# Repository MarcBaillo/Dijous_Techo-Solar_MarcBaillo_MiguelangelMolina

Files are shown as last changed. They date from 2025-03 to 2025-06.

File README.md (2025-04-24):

## Dijous_Techo-Solar_MarcBaillo_MiguelangelMolina
Proyecto de Herramientas de Diseño del Techo Solar (Jueves).

# Autores
- Miguelangel Molina(@MiaMoSaN)
- Marc Baillo (@MarcBaillo)

## Objectivos del proyecto

El objetivo que tenemos es conseguir diseñar un techo solar que estara formado por un microcontrolador, 2 motores que controlaran la apertura con final de carrera y el movimiento de la cortina, un sensor que evite atrapamientos y una luz ambiental producida por un LED RGB. Todo esto estara implementado en una PCB, pasando por las fases de diagrama de bloque, que luego pasar al esquematico y alfinal al layout, para luego evaluarlo y hacer unos presupuestos de cuanto valdra crear la placa.

## Requisitos i especificaciones:

- Diseño integral de un techo solar controlado por microcontrolador.
- Implementación de un motor de apertura con final de carrera.
- Integración de un motor de la cortina.
- Luz ambiental RGB.
- Integración de un sensor digital para evitar que atrapamientos.

## Diagrama de bloque

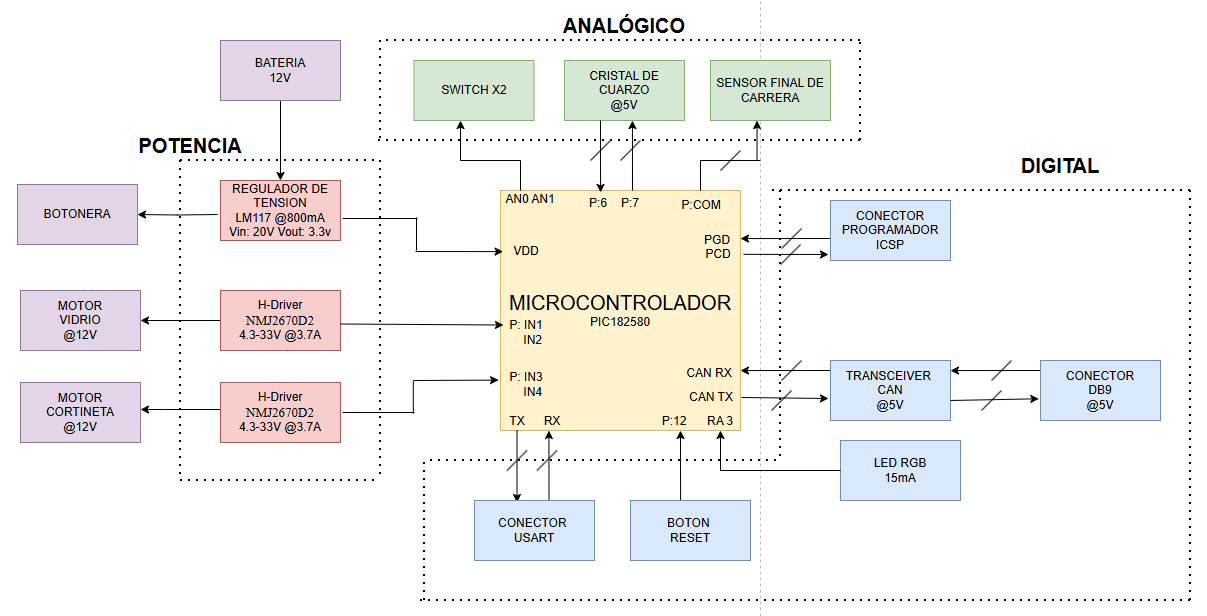
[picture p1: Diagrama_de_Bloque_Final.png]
Diagrama de Bloque


## Tabla de componentes
| Descripción | Manufacturer Number | Descripción | Datasheet | Proveidor | Unidades | Precio Unitario |
|:---:|:---:|:---:|:---:|:---:|:---:|:---:|
| Microcontrolador | PIC18LF2580-I/SO | Procesador que actúa como cerebro de control del circuito | [Datasheet](https://ww1.microchip.com/downloads/aemDocuments/documents/OTH/ProductDocuments/DataSheets/39637d.pdf) | DigiKey | 1 | 9,2€ |
| Regulador de tensión | LM1117DT-3.3/NOPB  | Dispositivo que hace que la tensión de entrada pase de 12V a los que necesita el microcontrolador (3,3V) | [Datasheet](https://www.ti.com/lit/ds/symlink/lm1117.pdf?ts=1710745623625&ref_url=https%253A%252F%252Fwww.mouser.se%252F) | Mouser Electronics | 1 | 1,61€ |
| Conector | DB9  | Se ocupa de la conexión entre diferentes dispositivos |[Datasheet](https://www.mouser.es/datasheet/2/18/1/Cable_Glands_and_Cord_Grips-806485.pdf) | Mouser Electronics | 1 | 19,08€ |
| Oscilador | ECS-80-8-30-JGN-TR | Genera ondas de señales precisas| [Datasheet](https://www.mouser.es/datasheet/2/122/ecx_53r-1775695.pdf) | Mouser Electronics | 1 | 0,53€ |
| H-Driver | DRV8231ADDAR  | controla el sentido de giro de un motor | [Datasheet](https://www.ti.com/lit/ds/symlink/drv8231a.pdf?ts=1710753914026&ref_url=https%253A%252F%252Fwww.mouser.de%252F) | Mouser Electronics | 1 | 1,24€ |
| Transceiver | 	TCAN332DR  | Dispositivo que recibe y trtransmite datos |[Datasheet](https://www.ti.com/lit/ds/symlink/tcan332g.pdf?ts=1710924087476&ref_url=https%253A%252F%252Fwww.mouser.de%252F) | DigiKey | 1 | 2,83€ |
| LED RGB | LB Q39G-N1OO-35-1-5-R18  | LED que da luz ambiental al coche |[Datasheet](https://look.ams-osram.com/m/6e36864d019f51d4/original/LB-Q39G.pdf) | DigiKey | 1 | 0,2€ |
| Motor | D4387-12-ME  | Motores para poder abrir y cerrar el cristal o la cortina del techo | [Datasheet](https://transmotec.es/Download/Catalog/Transmotec-EN-DC-12W-450W-2022.pdf) | Transmotec | 2 | 345€ |
| Switch | SS-01GPD  | Dispositivos que controlan cuando es el final de carrera | [Datasheet](https://www.mouser.es/datasheet/2/307/en_ss-1509069.pdf) | Mouser Electronics | 1 | 1,27€ |
| Pulsador | MPB01-1B00-S-D  | Dispositivo que permite controlar el motor para que el techo o cortina se abra o se cierre  | [Datasheet](https://www.mouser.es/datasheet/2/670/mpb01-2474754.pdf) | Mouser Electronics | 2 | 3,14€ |
| Conector | ICSP  | Sirve para comunicarse con el exterior para programar el microcontrolador | [Datasheet](https://ww1.microchip.com/downloads/en/DeviceDoc/30277d.pdf) | DigiKey | 2 | 1,52€ |

## Historial de canvis 

| Data | Autor | Descripció |
|:---:|:---:|:---:|
| 20-03-2025 | Marc y Miguel | Creado el proyecto y escogido el diseño que se trabajara (Techo Solar) |
| 20-03-2025 | Marc y Miguel | Elección de componentes y presentación del proyecto (Sesión 1) |
| 20-03-2025 | Marc y Miguel | Creación de Diagrama de Bloque |
| 23-03-2025 | Marc | Cadlab y GitHub creado |
| 24-03-2025 | Miguel | Creación del Esquematico |
| 25-03-2025 | Marc | Simulaciones hechas |
| 26-03-2025 | Miguel | Modificación Diagrama de Bloque |
| 27-03-2025 | Marc | Creació del README |
| 27-03-2025 | Marc y Miguel | Modificación presentación proyecto (Sesión 2) |
| 31-03-2025 | Miguel | Creación Layout |
| 02-04-2025 | Marc | Simulación ADC hecha |
| 03-04-2025 | Miguel y Marc | Modificación presentación proyecto (Sesión 3) |
| 03-04-2025 | Miguel | Corrección errores Layout y Esquematicos |
| 09-04-2025 | Marc | Modificación Layout (acabar de poner vista 3D y packages bien) |
| 09-04-2025 | Marc |  Modificación presentación proyecto (Sesión 4)  |
| 10-04-2025 | Marc y Miguel |  Modificación presentación proyecto (Sesión 4)  |
| 10-04-2025 | Miguel | Finalización del Esquematico y del Layout |
| 10-04-2025 | Miguel | Reglas de diseño definidas |
| 23-04-2025 | Marc | Presupuesto hecho |
| 24-04-2025 | Miguel y Marc | Modificación presentación proyecto (Sesión presentación proyecto final) |

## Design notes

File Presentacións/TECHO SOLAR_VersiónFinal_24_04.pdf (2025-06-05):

# Proyecto: Techo Solar

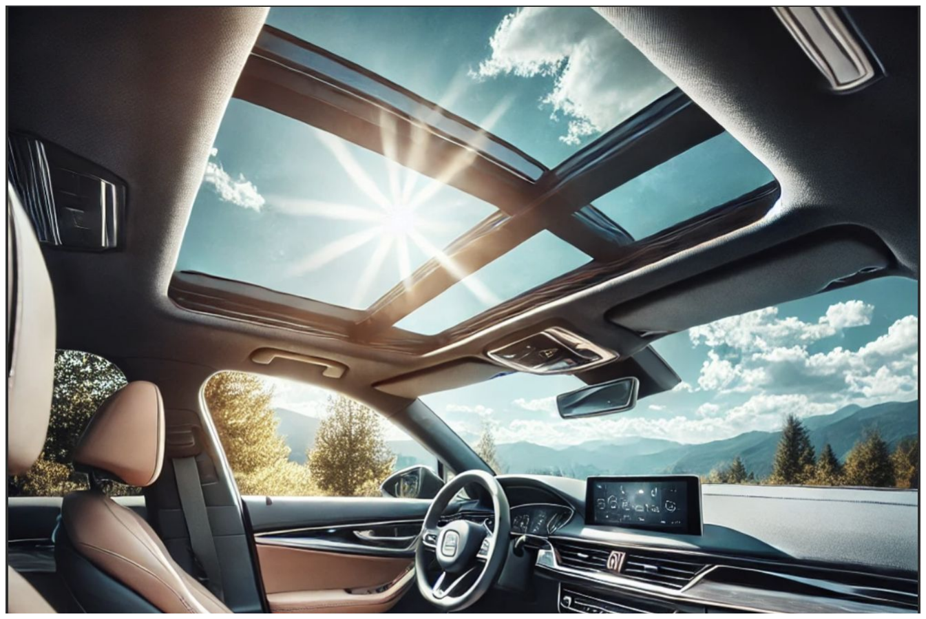
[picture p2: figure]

| Miguelangel Molina Marc Baillo

### Curso 2025 Grupo C

## El techo solar es un panel de vidrio o material translúcido ubicado en el techo de un automóvil que permite la entrada de luz y aire al interior del vehículo

## OBJETIVOS

Diseño integral de un techo solar controlado por microcontrolador.

Implementación de un motor de apertura con final de carrera.

Integración de un motor de la cortina.

Luz ambiental RGB.

Integración de un sensor digital para evitar que atrapamientos.

# Proyecto: Diseño del Techo Solar del coche

## DIAGRAMA DE BLOQUES

# Proyecto: Diseño del Techo Solar del coche

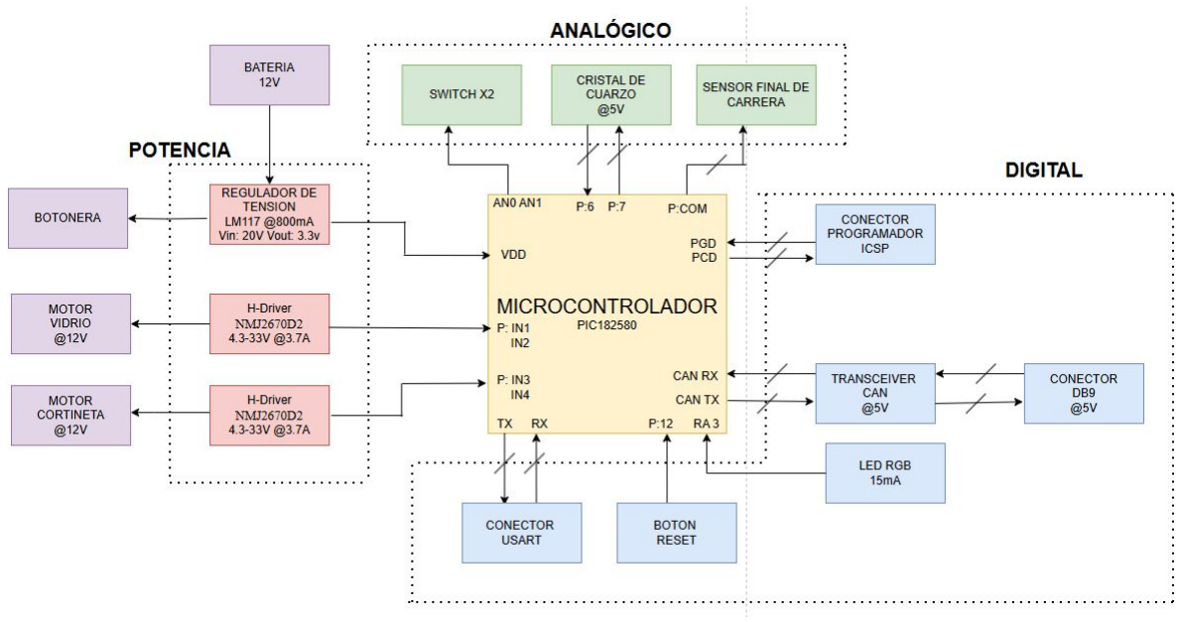
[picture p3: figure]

# Componentes

TIPO | COMPONENTES | DESCRIPCIÓN
POWER | | Las redes de potencia se refieren a los sistemas eléctricos que suministran energía eléctrica a los
ANALOG | Oscilador, Sensor final de carrera, | La información se transmite en forma de señales analógicas.
DIGITAL | Led Conectores de comunicación (Transceiver, db9, …) Microcontrolador, | Transmiten los datos en forma de

Driver motor
Regulador de tensión,
consumidores.

Botonera

Sensor de movimiento

bits, típicamente como 0 o 1.

# Proyecto: Diseño del Techo Solar del coche

# Proyecto: Diseño del Techo Solar del coche

COMPONENTES | UTILIDAD | CARACTERÍSTICAS | MODELO | DATASHEETS
Microcontrolador | Circuito programable que actuará como centro de control de todo el circuito. | Vmin = 2V Vmax = 5,5V I = 250mA
Regulador de tensión | Dispositivo que mantendrá o regulará un nivel de tensión constante. | Vmin = 3,3V Vmàx = 20V I = 1.2A
Conector | Conector que sirve para la
Oscilador | Permite la generación de señales
H-Driver | Permitirá el control de los motores. | V=4.3-33V Power supply = -0.5-35V Imax = 0-3.7A
PIC18LF2580 | Micro/datasheet (https://ww1.microchip.com/downloads/aemDocuments/documents/OTH/ProductDocuments/DataSheets/39637d.pdf)
LM1117CST-3.3 | Reg/datasheet (https://eu.mouser.com/datasheet/2/609/1117fd-2953685.pdf)
comunicación entre dispositivos. | — | DB9 | Conn/datasheet (https://www.mouser.es/datasheet/2/18/1/Cable_Glands_and_Cord_Grips-806485.pdf)
eléctricas de una alta precisión. | Frecuencia = 8 MHz | ECS-80-8-30-JGN-TR | Osc/datasheet (https://www.mouser.es/datasheet/2/122/ecx_53r-1775695.pdf)
L293DD | Driver/datasheet (https://www.alldatasheet.com/datasheet-pdf/view/22433/STMICROELECTRONICS/L293DD.html)

COMPONENTES | UTILIDAD | CARACTERÍSTICAS | MODELO | DATASHEETS
Transceiver | Se encarga de recibir datos y transmitirlos. | Vmin = 3V
Vmax = 3.6V | TCAN 332x | Tran/datasheet (https://www.ti.com/lit/ds/symlink/tcan332g.pdf?ts=1710924087476)
LED RGB | LED que dará luz ambiente | Forward current = 15 mA | LBQ39G | LED/datasheet (https://look.ams-osram.com/m/6e36864d019f51d4/original/LB-Q39G.pdf)
Motor cortina | Motor externo encargado de abrir o cerrar la cortina | Voltage=12 V
Motor final de carrera | Motor externo encargado de abrir o cerrar el techo | Voltage=12 V
I=2A | D4387-12-ME | Motor/datasheet (https://transmotec.es/Download/Catalog/Transmotec-EN-DC-12W-450W-2022.pdf)
I=2A | D4387-12-ME | Motor/datasheet (https://transmotec.es/Download/Catalog/Transmotec-EN-DC-12W-450W-2022.pdf)

# Proyecto: Diseño del Techo Solar del coche

COMPONENTES | UTILIDAD | CARACTERÍSTICAS | MODELO | DATASHEETS
Switch | Para el final de carrera. | 0.1A to 10.1A | B3F-4050 | Interr/datasheet (https://www.mouser.es/datasheet/2/307/en_b3f-1664344.pdf)
Pulsador cortina | Pulsador para abrir y cerrar
Conector | Para programar el
Pulsador cristal | Pulsador para abrir y cerrar
la cortina. | 14 mA | MPB01-1B33-S- D
Puls/datasheet (https://eu.mouser.com/datasheet/2/1628/mpb01-3510627.pdf)
microcontrolador. | — | ICSP | Conn/datasheet (https://ww1.microchip.com/downloads/en/DeviceDoc/30277d.pdf)

# Proyecto: Diseño del Techo Solar del coche

el cristal del techo. | 14 mA | MPB01-1B33-S- D
Puls/datasheet (https://www.mouser.es/datasheet/2/670/mpb01-2474754.pdf)

# Proyecto: Simulación LTSpice Motor DC

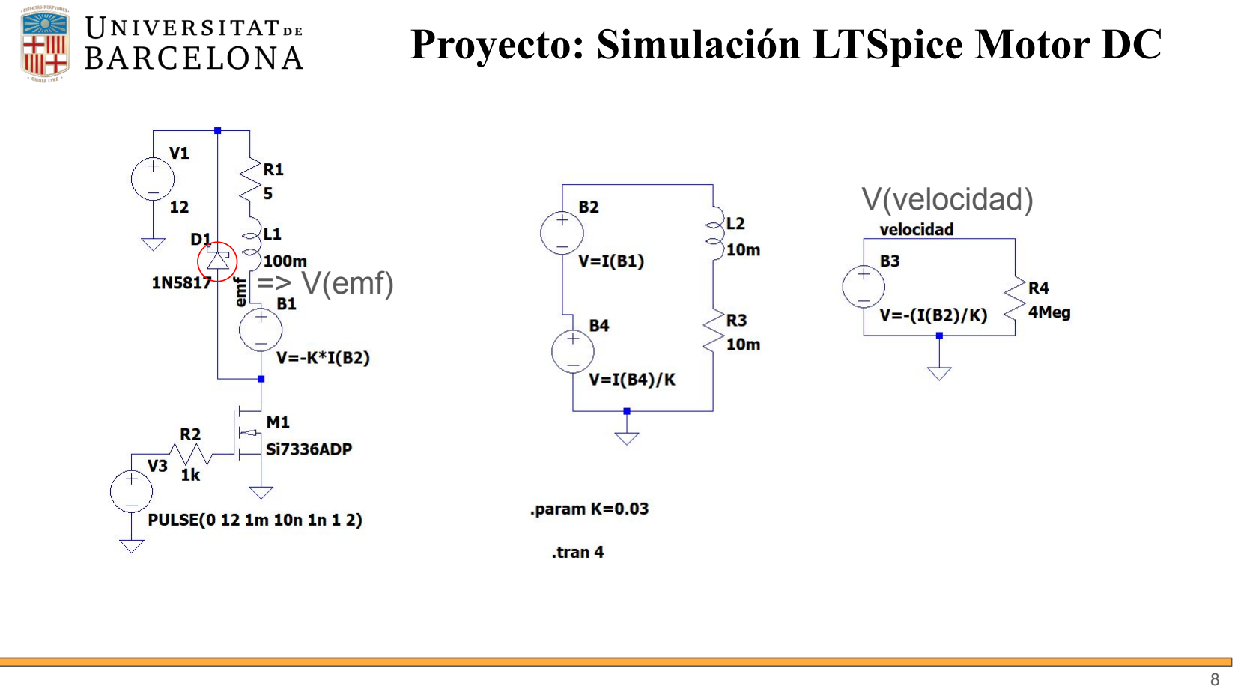
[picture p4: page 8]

## => V(emf)

## V(velocidad)

# Proyecto: Simulación LTSpice Motor DC

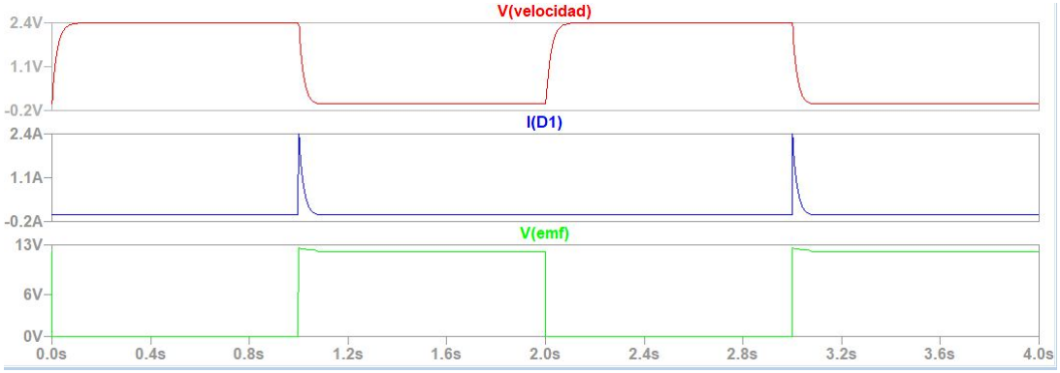
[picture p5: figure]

## Proyecto: Simulación LTSpice Regulador de Tensión

## Vin

## Vout

## Vout ampliado

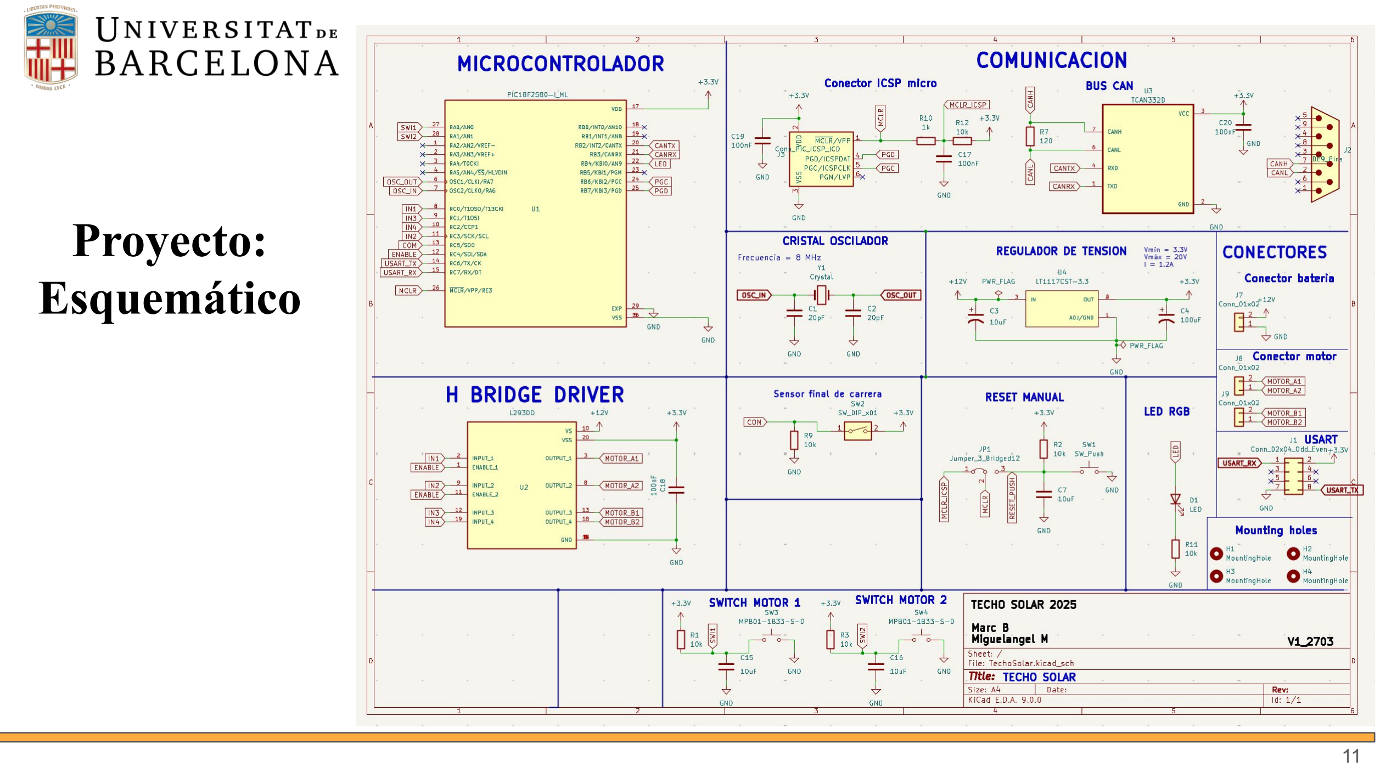
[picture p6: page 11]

# Proyecto: Esquemático

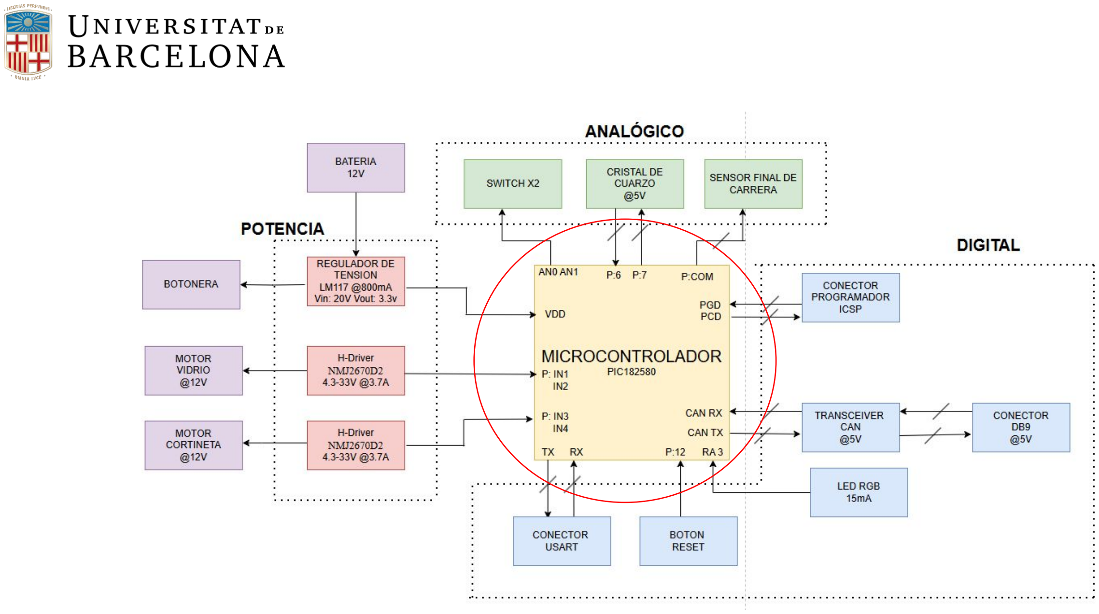
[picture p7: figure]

# Microcontrolador: PIC18LF2580

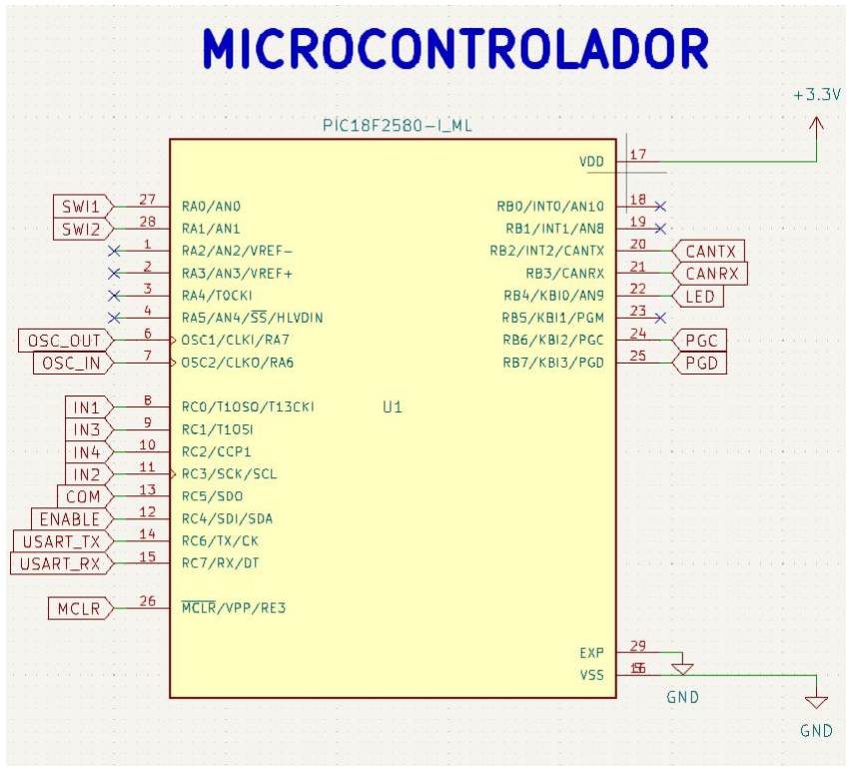
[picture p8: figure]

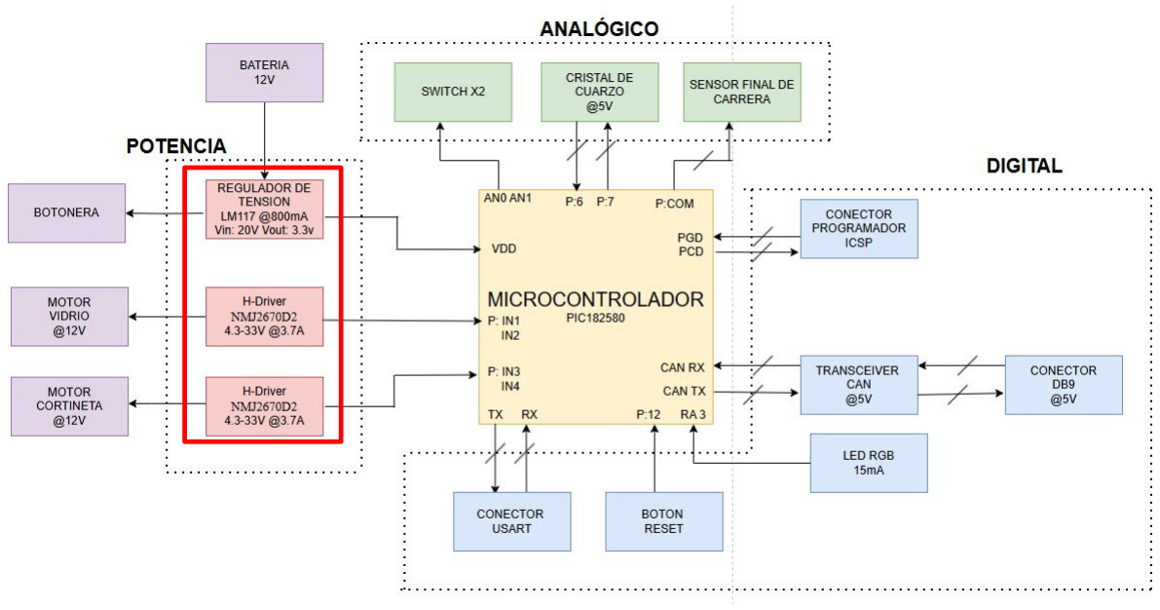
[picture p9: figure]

# Potencia

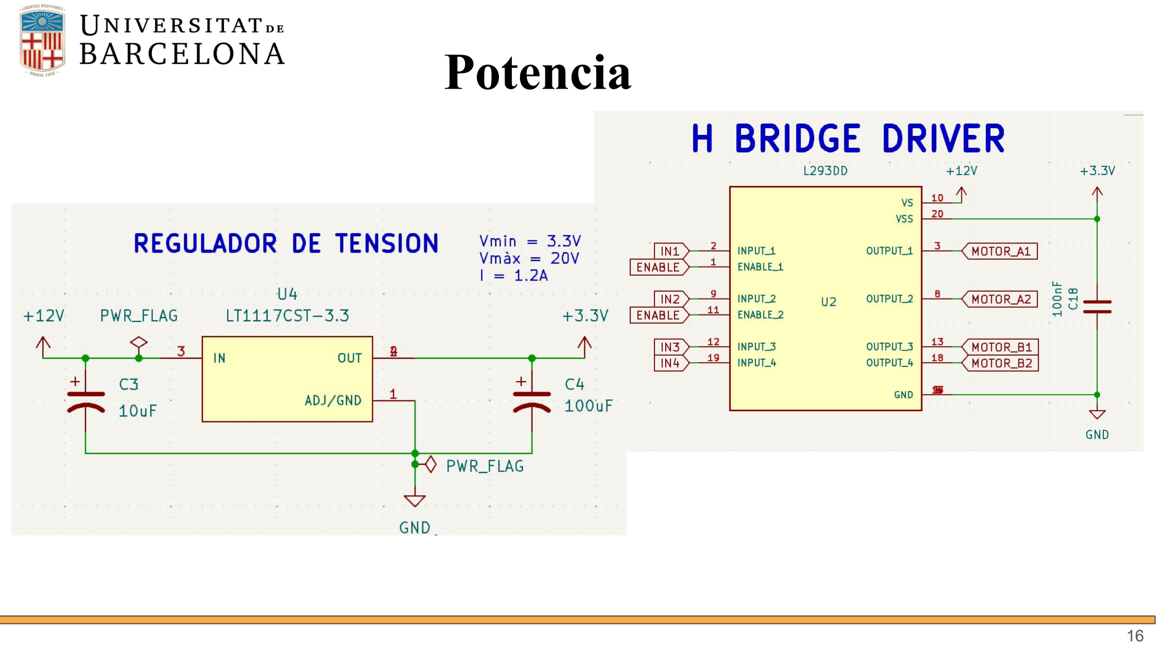
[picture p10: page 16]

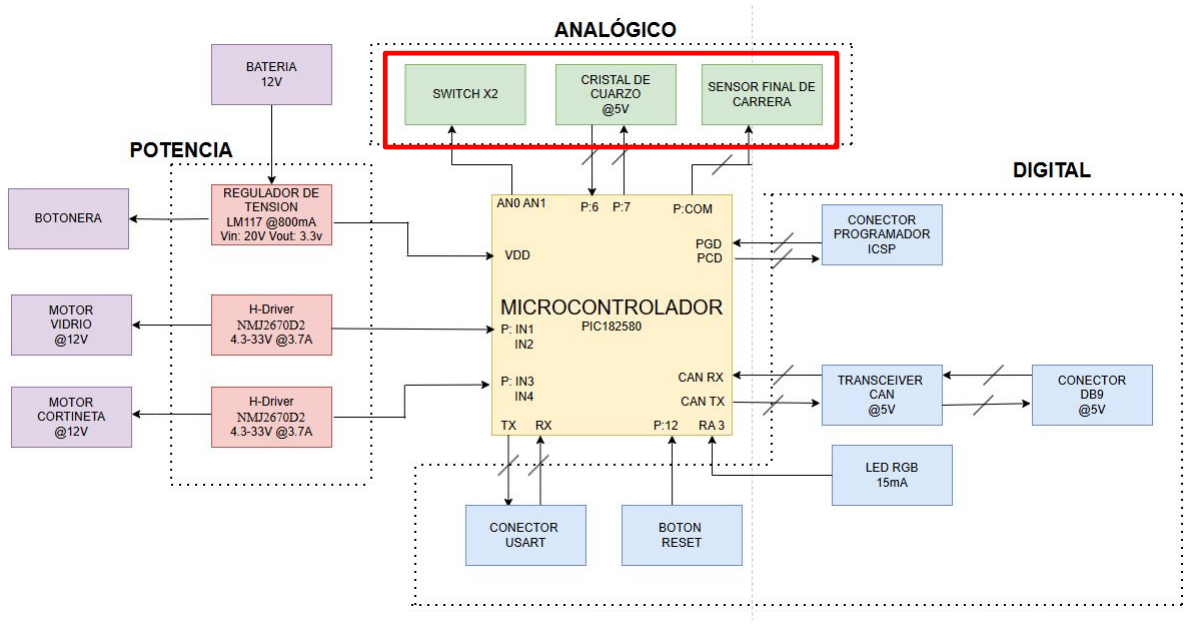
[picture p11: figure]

# Analogico: oscilador y sensor

# Analogico: Switch de los 2 motores

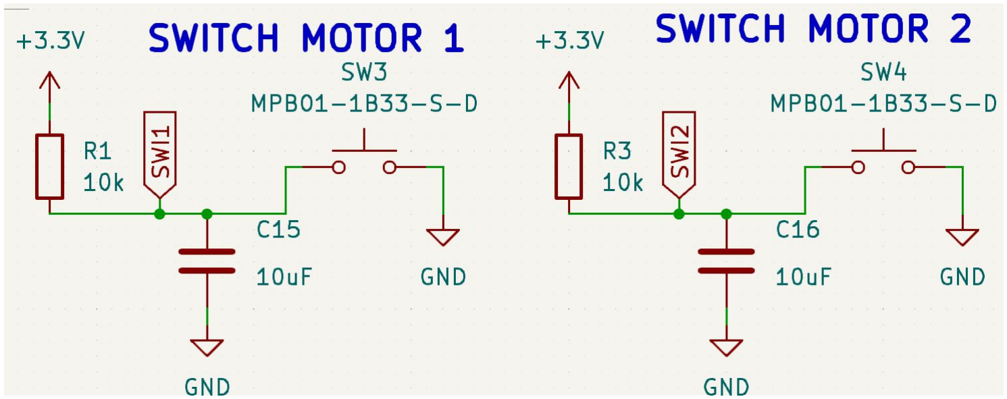
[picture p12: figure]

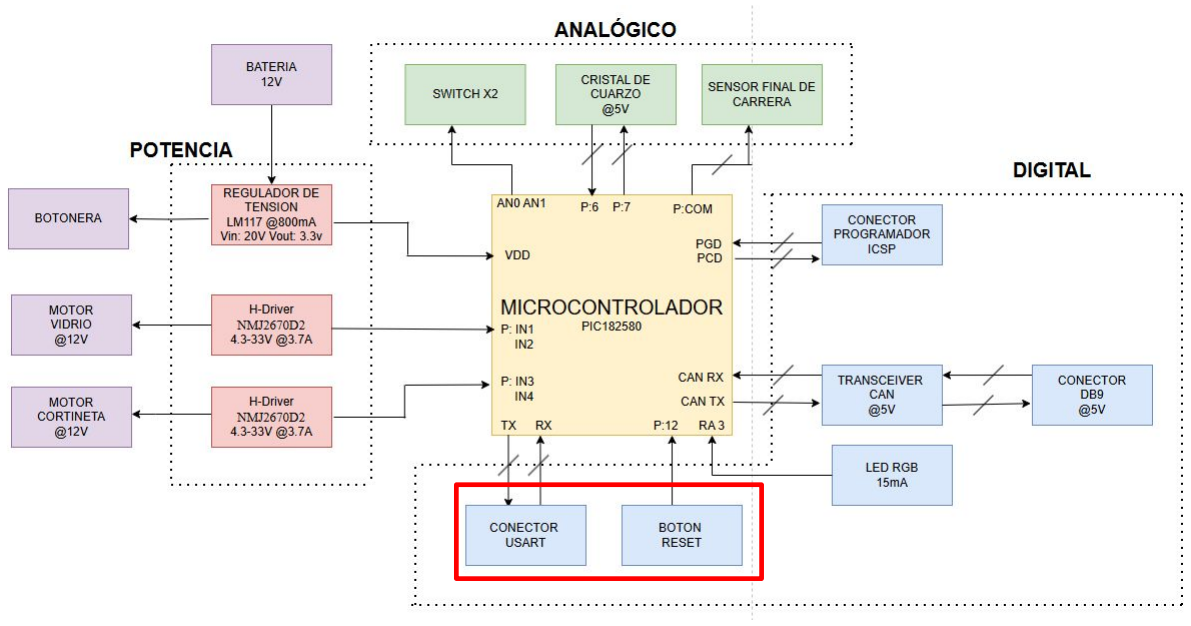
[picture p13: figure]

# Digital: boton reset y conector USART

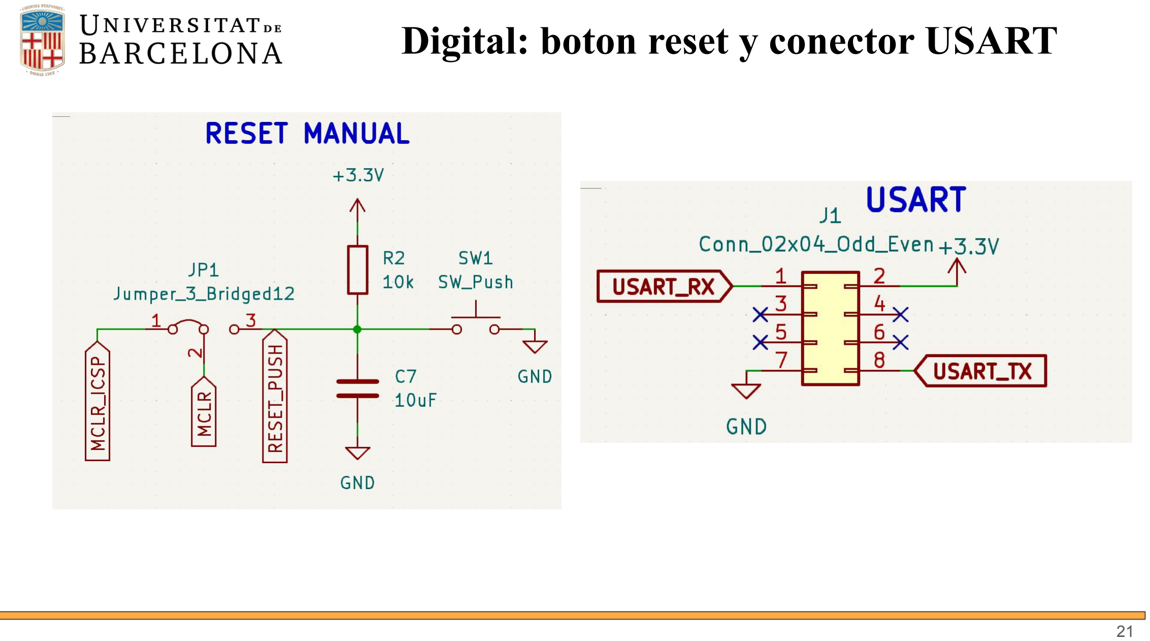
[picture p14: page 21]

# Digital: LED RGB

# Proyecto: Diseño del Techo Solar del coche

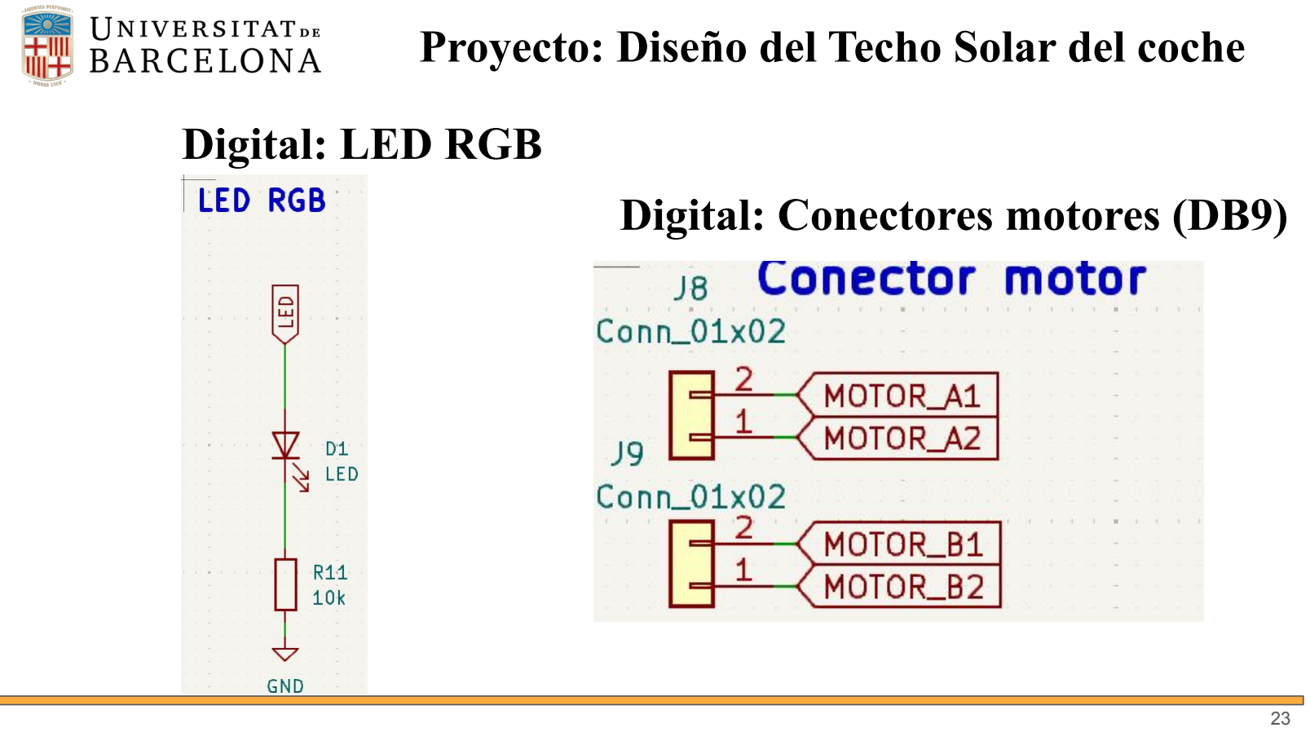
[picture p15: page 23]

# Digital: Conectores motores (DB9)

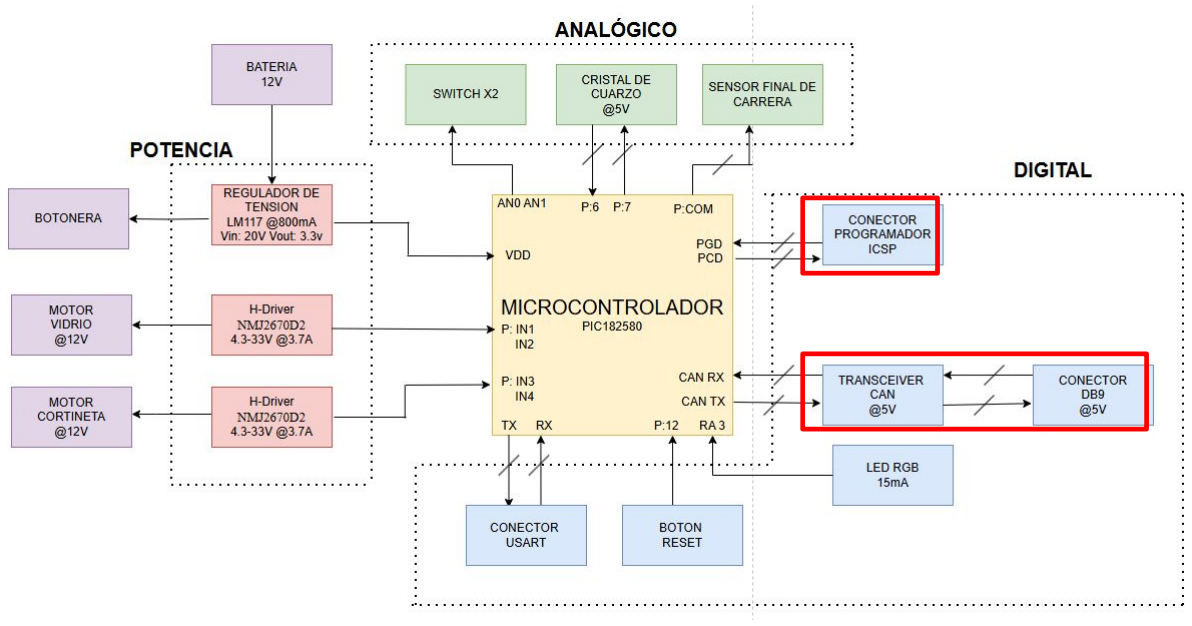
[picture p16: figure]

# Digital (COMUNICACIÓN)

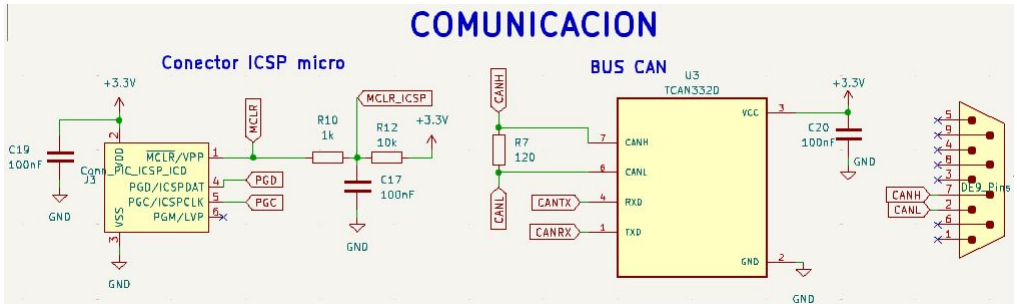
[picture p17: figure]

# DRC

# Proyecto: Diseño del Techo Solar del coche

# LAYOUT (actualizada) - versión final

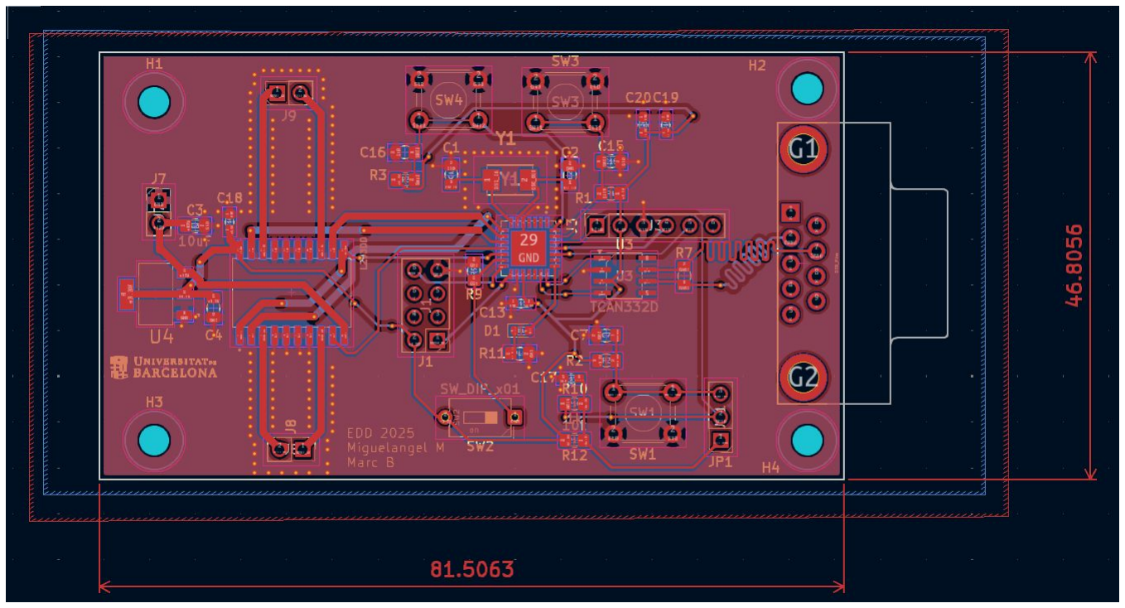
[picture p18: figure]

# Layout: capa TOP

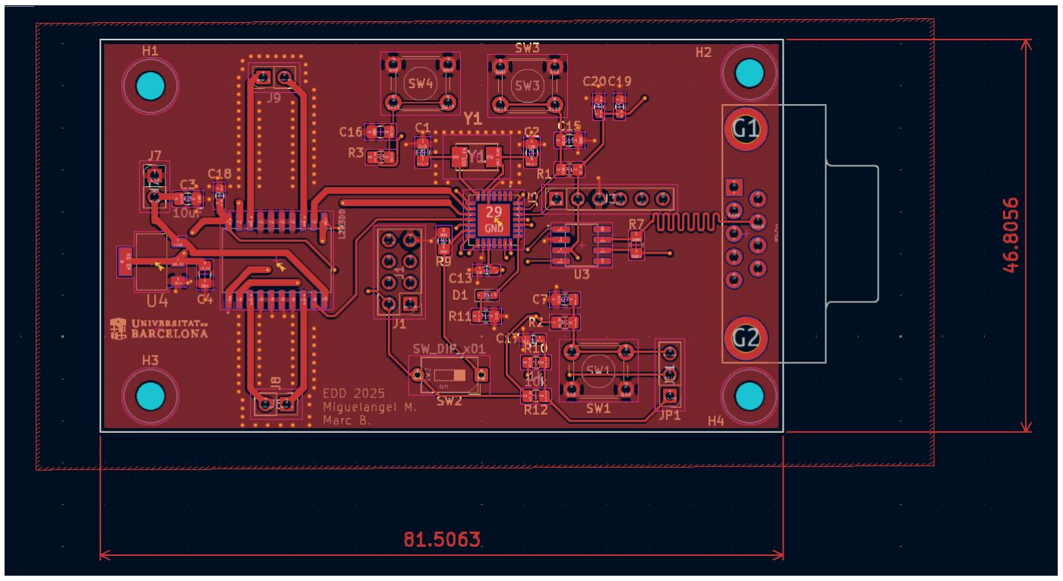
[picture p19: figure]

# Layout: capa BOTTOM

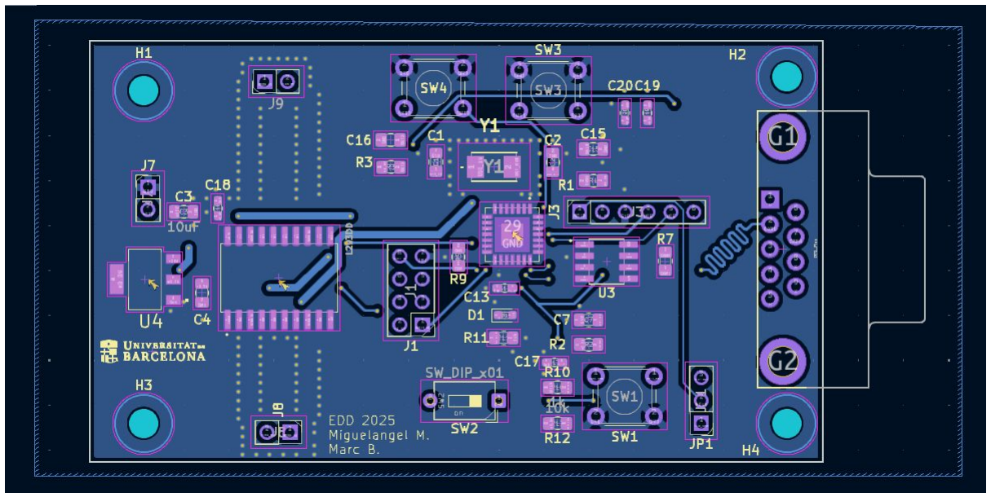
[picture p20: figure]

LAYOUT (03/04/2025) - v1.

# Proyecto: Diseño del Techo Solar del coche

# Vista en 3D (actualizada) - versión final

# Proyecto: Diseño del Techo Solar del coche

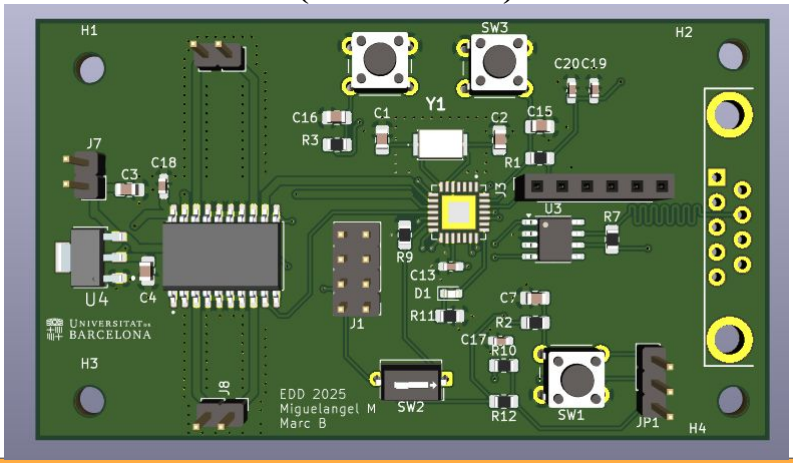
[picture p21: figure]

Vista en 3D (03/04/2025) - v1.

# Proyecto: Diseño del Techo Solar del coche

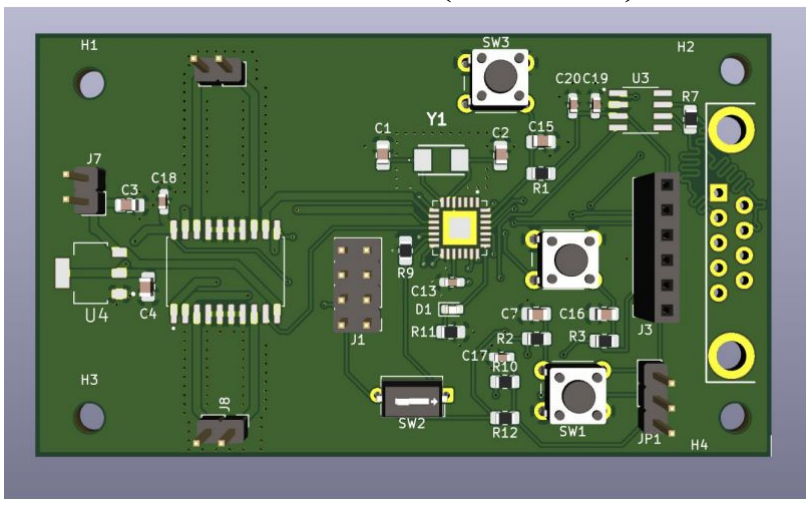
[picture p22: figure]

# DRC

# Proyecto: Diseño del Techo Solar del coche

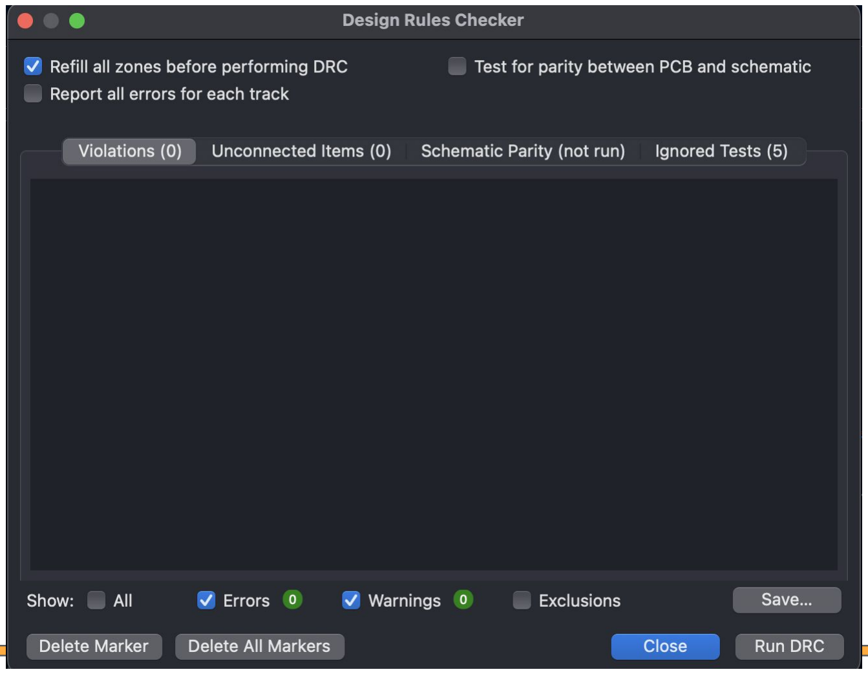
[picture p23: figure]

# Reglas de Diseño

## Las reglas de diseño las hemos sacado del fabricante: Safe

PCB.

# Proyecto: Diseño del Techo Solar del coche

# Presupuesto Proyecto

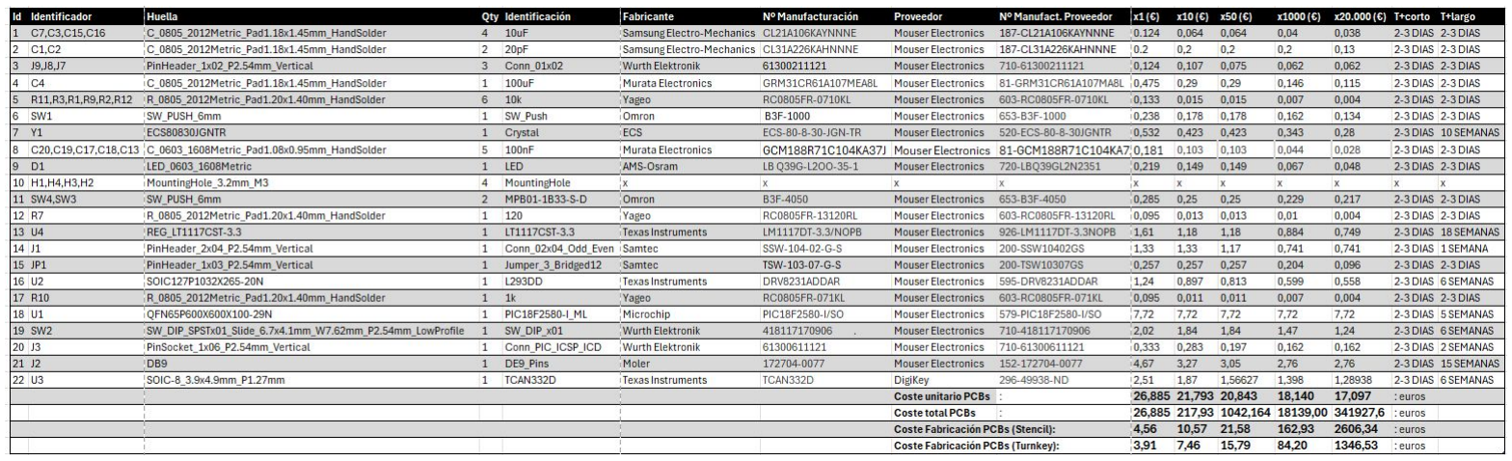
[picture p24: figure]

# Presupuesto Proyecto Resumen

Precio / Unidad | x1 (€) | x10 (€) | x50 (€) | x1000 (€) | x20000 (€)
Coste Unitario PCB | 26,885 € | 21,793 € | 20,843 € | 18,14 € | 17,097 €
Coste Total PCBs | 26,885 € | 217,93 € | 1042,16 € | 18139 € | 341927,6 €
Coste Fabricación PCBs | 3,56 € | 10,57 € | 21,58€ | 84,20 | 1348,53

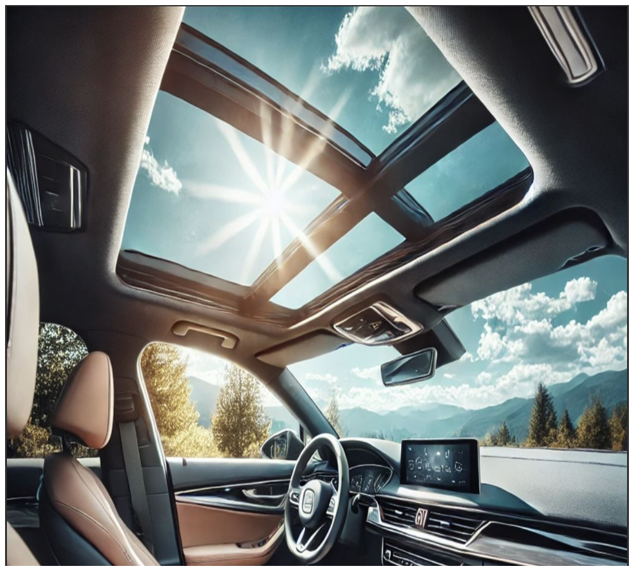
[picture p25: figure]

# Asignaciones del Software para el microcontrolador

Pines de E/S para la gestión de los componentes para el microcontrolador

Interfaz SPI para la comunicación con el controlador

Interfaz CAN para las comunicaciones

# Conclusiones

Diseño integral de un techo solar controlado por microcontrolador.

Implementación de un motor de apertura con final de carrera y led ambiental RGB.

# Proyecto: Diseño del Techo Solar del coche

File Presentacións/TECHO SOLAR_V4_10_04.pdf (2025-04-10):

# Proyecto: Techo Solar


| Miguelangel Molina Marc Baillo

### Curso 2025 Grupo C

## El techo solar es un panel de vidrio o material translúcido ubicado en el techo de un automóvil que permite la entrada de luz y aire al interior del vehículo

## OBJETIVOS


Diseño integral de un techo solar controlado por microcontrolador.

Implementación de un motor de apertura con final de carrera.

Integración de un motor de la cortina.

Luz ambiental RGB.

Integración de un sensor digital para evitar que atrapamientos.

# Proyecto: Diseño del Techo Solar del coche

## DIAGRAMA DE BLOQUES

# Proyecto: Diseño del Techo Solar del coche

# Componentes

TIPO | COMPONENTES | DESCRIPCIÓN
POWER | | Las redes de potencia se refieren a los sistemas eléctricos que suministran energía eléctrica a los
ANALOG | Oscilador, Sensor final de carrera, | La información se transmite en forma de señales analógicas.
DIGITAL | Led Conectores de comunicación (Transceiver, db9, …) Microcontrolador, | Transmiten los datos en forma de

Driver motor
Regulador de tensión,
consumidores.

Botonera

Sensor de movimiento

bits, típicamente como 0 o 1.

# Proyecto: Diseño del Techo Solar del coche

# Proyecto: Diseño del Techo Solar del coche

COMPONENTES | UTILIDAD | CARACTERÍSTICAS | MODELO | DATASHEETS
Microcontrolador | Circuito programable que actuará como centro de control de todo el circuito. | Vmin = 2V Vmax = 5,5V I = 250mA
Regulador de tensión | Dispositivo que mantendrá o regulará un nivel de tensión constante. | Vmin = 3,3V Vmàx = 20V I = 1.2A
Conector | Conector que sirve para la
Oscilador | Permite la generación de señales
H-Driver | Permitirá el control de los motores. | V=4.3-33V Power supply = -0.5-35V Imax = 0-3.7A
PIC18LF2580 | Micro/datasheet (https://ww1.microchip.com/downloads/aemDocuments/documents/OTH/ProductDocuments/DataSheets/39637d.pdf)
LM1117CST-3.3 | Reg/datasheet (https://eu.mouser.com/datasheet/2/609/1117fd-2953685.pdf)
comunicación entre dispositivos. | — | DB9 | Conn/datasheet (https://www.mouser.es/datasheet/2/18/1/Cable_Glands_and_Cord_Grips-806485.pdf)
eléctricas de una alta precisión. | Frecuencia = 8 MHz | ECS-80-8-30-JGN-TR | Osc/datasheet (https://www.mouser.es/datasheet/2/122/ecx_53r-1775695.pdf)
L293DD | Driver/datasheet (https://www.alldatasheet.com/datasheet-pdf/view/22433/STMICROELECTRONICS/L293DD.html)

COMPONENTES | UTILIDAD | CARACTERÍSTICAS | MODELO | DATASHEETS
Transceiver | Se encarga de recibir datos y transmitirlos. | Vmin = 3V
Vmax = 3.6V | TCAN 332x | Tran/datasheet (https://www.ti.com/lit/ds/symlink/tcan332g.pdf?ts=1710924087476)
LED RGB | LED que dará luz ambiente | Forward current = 15 mA | LBQ39G | LED/datasheet (https://look.ams-osram.com/m/6e36864d019f51d4/original/LB-Q39G.pdf)
Motor cortina | Motor externo encargado de abrir o cerrar la cortina | Voltage=12 V
Motor final de carrera | Motor externo encargado de abrir o cerrar el techo | Voltage=12 V
I=2A | D4387-12-ME | Motor/datasheet (https://transmotec.es/Download/Catalog/Transmotec-EN-DC-12W-450W-2022.pdf)
I=2A | D4387-12-ME | Motor/datasheet (https://transmotec.es/Download/Catalog/Transmotec-EN-DC-12W-450W-2022.pdf)

# Proyecto: Diseño del Techo Solar del coche

COMPONENTES | UTILIDAD | CARACTERÍSTICAS | MODELO | DATASHEETS
Switch | Para el final de carrera. | 0.1A to 10.1A | SS-01GPD | Interr/datasheet (https://www.mouser.es/datasheet/2/307/en_ss-1509069.pdf)
Pulsador cortina | Pulsador para abrir y cerrar
Conector | Para programar el
Pulsador cristal | Pulsador para abrir y cerrar
la cortina. | 14 mA | MPB01-1B33-S- D
Puls/datasheet (https://eu.mouser.com/datasheet/2/1628/mpb01-3510627.pdf)
microcontrolador. | — | ICSP | Conn/datasheet (https://ww1.microchip.com/downloads/en/DeviceDoc/30277d.pdf)

# Proyecto: Diseño del Techo Solar del coche

el cristal del techo. | 14 mA | MPB01-1B33-S- D
Puls/datasheet (https://www.mouser.es/datasheet/2/670/mpb01-2474754.pdf)

# Proyecto: Simulación LTSpice Motor DC


## => V(emf)

## V(velocidad)

# Proyecto: Simulación LTSpice Motor DC


## Proyecto: Simulación LTSpice Regulador de Tensión

## Vin


## Vout

## Vout ampliado

# Proyecto: Esquemático


# Microcontrolador: PIC18LF2580



# Potencia


# Analogico: oscilador y sensor


# Analogico: Switch de los 2 motores


# Digital: boton reset y conector USART




# Digital: LED RGB

# Digital (COMUNICACIÓN)


# Digital: Conectores motores (DB9)


# DRC


LAYOUT (03/04/2025) - v1.


# LAYOUT (actualizada) - versión final

# Layout: capa TOP


# Layout: capa BOTTOM


Vista en 3D (03/04/2025) - v1.


# Vista en 3D (actualizada) - versión final

# DRC


# Reglas de Diseño


## Las reglas de diseño las hemos sacado del fabricante: Safe

PCB.

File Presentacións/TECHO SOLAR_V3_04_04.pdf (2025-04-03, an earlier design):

# Proyecto: Techo Solar


| Miguelangel Molina Marc Baillo

### Curso 2025 Grupo C

## El techo solar es un panel de vidrio o material translúcido ubicado en el techo de un automóvil que permite la entrada de luz y aire al interior del vehículo

## OBJETIVOS


Diseño integral de un techo solar controlado por microcontrolador.

Implementación de un motor de apertura con final de carrera.

Integración de un motor de la cortina.

Luz ambiental RGB.

Integración de un sensor digital para evitar que atrapamientos.

# Proyecto: Diseño del Techo Solar del coche

## DIAGRAMA DE BLOQUES

# Proyecto: Diseño del Techo Solar del coche


# Componentes

TIPO | COMPONENTES | DESCRIPCIÓN
POWER | | Las redes de potencia se refieren a los sistemas eléctricos que suministran energía eléctrica a los
ANALOG | Oscilador, Sensor final de carrera, | La información se transmite en forma de señales analógicas.
DIGITAL | Led Conectores de comunicación (Transceiver, db9, …) Microcontrolador, | Transmiten los datos en forma de

Driver motor
Regulador de tensión,
consumidores.

Botonera

Sensor de movimiento

bits, típicamente como 0 o 1.

# Proyecto: Diseño del Techo Solar del coche

# Proyecto: Diseño del Techo Solar del coche

COMPONENTES | UTILIDAD | CARACTERÍSTICAS | MODELO | DATASHEETS
Microcontrolador | Circuito programable que actuará como centro de control de todo el circuito. | Vmin = 2V Vmax = 5,5V I = 250mA
Regulador de tensión | Dispositivo que mantendrá o regulará un nivel de tensión constante. | Vmin = 3,3V Vmàx = 20V I = 1.2A
Conector | Conector que sirve para la
Oscilador | Permite la generación de señales
H-Driver | Permitirá el control de los motores. | V=4.3-33V Power supply = -0.5-35V Imax = 0-3.7A
PIC18LF2580 | Micro/datasheet (https://ww1.microchip.com/downloads/aemDocuments/documents/OTH/ProductDocuments/DataSheets/39637d.pdf)
LM1117CST-3.3 | Reg/datasheet (https://eu.mouser.com/datasheet/2/609/1117fd-2953685.pdf)
comunicación entre dispositivos. | — | DB9 | Conn/datasheet (https://www.mouser.es/datasheet/2/18/1/Cable_Glands_and_Cord_Grips-806485.pdf)
eléctricas de una alta precisión. | Frecuencia = 8 MHz | ECS-80-8-30-JGN-TR | Osc/datasheet (https://www.mouser.es/datasheet/2/122/ecx_53r-1775695.pdf)
L293DD | Driver/datasheet (https://www.alldatasheet.com/datasheet-pdf/view/22433/STMICROELECTRONICS/L293DD.html)

COMPONENTES | UTILIDAD | CARACTERÍSTICAS | MODELO | DATASHEETS
Transceiver | Se encarga de recibir datos y transmitirlos. | Vmin = 3V
Vmax = 3.6V | TCAN 332x | Tran/datasheet (https://www.ti.com/lit/ds/symlink/tcan332g.pdf?ts=1710924087476)
LED RGB | LED que dará luz ambiente | Forward current = 15 mA | LBQ39G | LED/datasheet (https://look.ams-osram.com/m/6e36864d019f51d4/original/LB-Q39G.pdf)
Motor cortina | Motor externo encargado de abrir o cerrar la cortina | Voltage=12 V
Motor final de carrera | Motor externo encargado de abrir o cerrar el techo | Voltage=12 V
I=2A | D4387-12-ME | Motor/datasheet (https://transmotec.es/Download/Catalog/Transmotec-EN-DC-12W-450W-2022.pdf)
I=2A | D4387-12-ME | Motor/datasheet (https://transmotec.es/Download/Catalog/Transmotec-EN-DC-12W-450W-2022.pdf)

# Proyecto: Diseño del Techo Solar del coche

COMPONENTES | UTILIDAD | CARACTERÍSTICAS | MODELO | DATASHEETS
Switch | Para el final de carrera. | 0.1A to 10.1A | SS-01GPD | Interr/datasheet (https://www.mouser.es/datasheet/2/307/en_ss-1509069.pdf)
Pulsador cortina | Pulsador para abrir y cerrar
Conector | Para programar el
Pulsador cristal | Pulsador para abrir y cerrar
la cortina. | 14 mA | MPB01-1B33-S- D
Puls/datasheet (https://eu.mouser.com/datasheet/2/1628/mpb01-3510627.pdf)
microcontrolador. | — | ICSP | Conn/datasheet (https://ww1.microchip.com/downloads/en/DeviceDoc/30277d.pdf)

# Proyecto: Diseño del Techo Solar del coche

el cristal del techo. | 14 mA | MPB01-1B33-S- D
Puls/datasheet (https://www.mouser.es/datasheet/2/670/mpb01-2474754.pdf)

# Proyecto: Simulación LTSpice Motor DC

## => V(emf)

## V(velocidad)

# Proyecto: Simulación LTSpice Motor DC


## Proyecto: Simulación LTSpice Regulador de Tensión

## Vin


## Vout

## Vout ampliado


# Proyecto: Esquemático


# Microcontrolador: PIC18LF2580


# Potencia



# Analogico: oscilador y sensor


# Analogico: Switch de los 2 motores



# Digital: boton reset y conector USART



# Digital: LED RGB


# Digital (COMUNICACIÓN)


# Digital: Conectores motores (DB9)


# DRC


# LAYOUT


# Layout: capa TOP

# Layout: capa BOTTOM


# Vista en 3D


# DRC


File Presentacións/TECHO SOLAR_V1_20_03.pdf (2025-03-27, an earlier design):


# Proyecto: Techo Solar


### Curso 2025

## Miguelangel Molina Marc Baillo


## El techo solar es un panel de vidrio o material translúcido ubicado en el techo de un automóvil que permite la entrada de luz y aire al interior del vehículo

## OBJETIVOS


Diseño integral de un techo solar controlado por microcontrolador.

Implementación de un motor de apertura con final de carrera.

Integración de un motor de la cortina.

Luz ambiental RGB.

Integración de un sensor digital para evitar que atrapamientos.

# Proyecto: Diseño del Techo Solar del coche

## DIAGRAMA DE BLOQUES

# Proyecto: Diseño del Techo Solar del coche


# Componentes

TIPO | COMPONENTES | DESCRIPCIÓN
POWER | | Las redes de potencia se refieren a los sistemas eléctricos que suministran energía eléctrica a los
ANALOG | Oscilador, Sensor final de carrera, | La información se transmite en forma de señales analógicas.
DIGITAL | Led Conectores de comunicación (Transceiver, db9, …) Microcontrolador, | Transmiten los datos en forma de

Driver motor
Regulador de tensión,
consumidores.

Botonera

Sensor de movimiento

bits, típicamente como 0 o 1.

# Proyecto: Diseño del Techo Solar del coche

# Proyecto: Diseño del Techo Solar del coche

COMPONENTES | UTILIDAD | CARACTERÍSTICAS | MODELO | DATASHEETS
Microcontrolador | Circuito programable que actuará como centro de control de todo el circuito. | Vmin = 2V Vmax = 5,5V I = 250mA
Regulador de tensión | Dispositivo que mantendrá o regulará un nivel de tensión constante. | Vmin = 3,3V Vmàx = 20V I = 1.2A
Conector | Conector que sirve para la
Oscilador | Permite la generación de señales
H-Driver | Permitirá el control de los motores. | V=4.3-33V Power supply = -0.5-35V Imax = 0-3.7A
PIC18FL2580 | Micro/datasheet (https://campusvirtual.ub.edu/pluginfile.php/9094043/mod_resource/content/0/PIC18F258.pdf)
LM1117 | Reg/datasheet (https://www.ti.com/lit/ds/symlink/lm1117.pdf?ts=1710745623625)
comunicación entre dispositivos. | — | DB9 | Conn/datasheet (https://www.mouser.es/datasheet/2/18/1/Cable_Glands_and_Cord_Grips-806485.pdf)
eléctricas de una alta precisión. | Frecuencia = 8 MHz | ECS-80-8-30-JGN-TR | Osc/datasheet (https://www.mouser.es/datasheet/2/122/ecx_53r-1775695.pdf)
NMJ2670D2 | Driver/datasheet (https://www.ti.com/lit/ds/symlink/drv8231a.pdf?ts=1710753914026)

COMPONENTES | UTILIDAD | CARACTERÍSTICAS | MODELO | DATASHEETS
ADC | Sensor que, al detectar el movimiento, evitará atrapamientos
Transceiver | Se encarga de recibir datos y transmitirlos. | Vmin = 3V

Vmin=2.5V
Vmax=3.6V
AD623ANZ | Sens/datasheet (https://www.vishay.com/docs/84937/vcnl3036x01.pdf)
Vmax = 3.6V | TCAN 332x | Tran/datasheet (https://www.ti.com/lit/ds/symlink/tcan332g.pdf?ts=1710924087476)
LED RGB | LED que dará luz ambiente | Forward current = 15 mA | LBQ39G | LED/datasheet (https://look.ams-osram.com/m/6e36864d019f51d4/original/LB-Q39G.pdf)
Motor cortina | Motor externo encargado de abrir o cerrar la cortina | Voltage=12 V
Motor final de carrera | Motor externo encargado de abrir o cerrar el techo | Voltage=12 V
I=2A | D4387-12-ME | Motor/datasheet (https://transmotec.es/Download/Catalog/Transmotec-EN-DC-12W-450W-2022.pdf)
I=2A | D4387-12-ME | Motor/datasheet (https://transmotec.es/Download/Catalog/Transmotec-EN-DC-12W-450W-2022.pdf)

# Proyecto: Diseño del Techo Solar del coche

COMPONENTES | UTILIDAD | CARACTERÍSTICAS | MODELO | DATASHEETS
Switch | Para el final de carrera. | 0.1A to 10.1A | SS-01GPD | Interr/datasheet (https://www.mouser.es/datasheet/2/307/en_ss-1509069.pdf)
Pulsador cortina | Pulsador para abrir y cerrar
Conector | Para programar el
Pulsador cristal | Pulsador para abrir y cerrar
la cortina. | 14 mA | MPB01-1B33-S- D
Puls/datasheet (https://www.mouser.es/datasheet/2/670/mpb01-2474754.pdf)
microcontrolador. | — | ICSP | Conn/datasheet (https://ww1.microchip.com/downloads/en/DeviceDoc/30277d.pdf)

# Proyecto: Diseño del Techo Solar del coche

el cristal del techo. | 14 mA | MPB01-1B33-S- D
Puls/datasheet (https://www.mouser.es/datasheet/2/670/mpb01-2474754.pdf)

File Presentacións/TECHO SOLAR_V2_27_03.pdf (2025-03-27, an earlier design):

# Proyecto: Techo Solar


### Curso 2025

## Miguelangel Molina Marc Baillo

## El techo solar es un panel de vidrio o material translúcido ubicado en el techo de un automóvil que permite la entrada de luz y aire al interior del vehículo

## OBJETIVOS


Diseño integral de un techo solar controlado por microcontrolador.

Implementación de un motor de apertura con final de carrera.

Integración de un motor de la cortina.

Luz ambiental RGB.

Integración de un sensor digital para evitar que atrapamientos.

# Proyecto: Diseño del Techo Solar del coche

## DIAGRAMA DE BLOQUES

# Proyecto: Diseño del Techo Solar del coche


# Componentes

TIPO | COMPONENTES | DESCRIPCIÓN
POWER | | Las redes de potencia se refieren a los sistemas eléctricos que suministran energía eléctrica a los
ANALOG | Oscilador, Sensor final de carrera, | La información se transmite en forma de señales analógicas.
DIGITAL | Led Conectores de comunicación (Transceiver, db9, …) Microcontrolador, | Transmiten los datos en forma de

Driver motor
Regulador de tensión,
consumidores.

Botonera

Sensor de movimiento

bits, típicamente como 0 o 1.

# Proyecto: Diseño del Techo Solar del coche

# Proyecto: Diseño del Techo Solar del coche

COMPONENTES | UTILIDAD | CARACTERÍSTICAS | MODELO | DATASHEETS
Microcontrolador | Circuito programable que actuará como centro de control de todo el circuito. | Vmin = 2V Vmax = 5,5V I = 250mA
Regulador de tensión | Dispositivo que mantendrá o regulará un nivel de tensión constante. | Vmin = 3,3V Vmàx = 20V I = 1.2A
Conector | Conector que sirve para la
Oscilador | Permite la generación de señales
H-Driver | Permitirá el control de los motores. | V=4.3-33V Power supply = -0.5-35V Imax = 0-3.7A
PIC18LF2580 | Micro/datasheet (https://ww1.microchip.com/downloads/aemDocuments/documents/OTH/ProductDocuments/DataSheets/39637d.pdf)
LM1117 | Reg/datasheet (https://www.ti.com/lit/ds/symlink/lm1117.pdf?ts=1710745623625)
comunicación entre dispositivos. | — | DB9 | Conn/datasheet (https://www.mouser.es/datasheet/2/18/1/Cable_Glands_and_Cord_Grips-806485.pdf)
eléctricas de una alta precisión. | Frecuencia = 8 MHz | ECS-80-8-30-JGN-TR | Osc/datasheet (https://www.mouser.es/datasheet/2/122/ecx_53r-1775695.pdf)
NMJ2670D2 | Driver/datasheet (https://www.ti.com/lit/ds/symlink/drv8231a.pdf?ts=1710753914026)

COMPONENTES | UTILIDAD | CARACTERÍSTICAS | MODELO | DATASHEETS
ADC | Sensor que, al detectar el movimiento, evitará atrapamientos
Transceiver | Se encarga de recibir datos y transmitirlos. | Vmin = 3V

Vmin=2.5V
Vmax=3.6V
AD623ANZ | Sens/datasheet (https://www.vishay.com/docs/84937/vcnl3036x01.pdf)
Vmax = 3.6V | TCAN 332x | Tran/datasheet (https://www.ti.com/lit/ds/symlink/tcan332g.pdf?ts=1710924087476)
LED RGB | LED que dará luz ambiente | Forward current = 15 mA | LBQ39G | LED/datasheet (https://look.ams-osram.com/m/6e36864d019f51d4/original/LB-Q39G.pdf)
Motor cortina | Motor externo encargado de abrir o cerrar la cortina | Voltage=12 V
Motor final de carrera | Motor externo encargado de abrir o cerrar el techo | Voltage=12 V
I=2A | D4387-12-ME | Motor/datasheet (https://transmotec.es/Download/Catalog/Transmotec-EN-DC-12W-450W-2022.pdf)
I=2A | D4387-12-ME | Motor/datasheet (https://transmotec.es/Download/Catalog/Transmotec-EN-DC-12W-450W-2022.pdf)

# Proyecto: Diseño del Techo Solar del coche

COMPONENTES | UTILIDAD | CARACTERÍSTICAS | MODELO | DATASHEETS
Switch | Para el final de carrera. | 0.1A to 10.1A | SS-01GPD | Interr/datasheet (https://www.mouser.es/datasheet/2/307/en_ss-1509069.pdf)
Pulsador cortina | Pulsador para abrir y cerrar
Conector | Para programar el
Pulsador cristal | Pulsador para abrir y cerrar
la cortina. | 14 mA | MPB01-1B33-S- D
Puls/datasheet (https://www.mouser.es/datasheet/2/670/mpb01-2474754.pdf)
microcontrolador. | — | ICSP | Conn/datasheet (https://ww1.microchip.com/downloads/en/DeviceDoc/30277d.pdf)

# Proyecto: Diseño del Techo Solar del coche

el cristal del techo. | 14 mA | MPB01-1B33-S- D
Puls/datasheet (https://www.mouser.es/datasheet/2/670/mpb01-2474754.pdf)

# Proyecto: Simulación LTSpice Motor DC


## => V(emf)

## V(velocidad)

# Proyecto: Simulación LTSpice Motor DC


## Proyecto: Simulación LTSpice Regulador de Tensión

## Vin


## Vout

## Vout ampliado


# Proyecto: Esquemático


# Microcontrolador: PIC18F2580



# Potencia



# Analogico: oscilador y sensor


# Analogico: Switch de los 2 motores



# Digital: boton reset y conector USART




# Digital: LED RGB


# Digital (COMUNICACIÓN)


# Digital: Conectores motores (DB9)




# Digital: ADC

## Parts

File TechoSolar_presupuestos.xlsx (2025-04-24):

Grupo C / Techo Solar
Marc Baillo
Miguelangel Molina
 | Id | Identificador | Huella | Qty | Identificación | Fabricante | Nº Manufacturación | Proveedor | Nº Manufact. Proveedor | x1 (€) | x10 (€) | x50 (€) | x1000 (€) | x20.000 (€) | T+corto | T+largo
 | 1 | C7,C3,C15,C16 | C_0805_2012Metric_Pad1.18x1.45mm_HandSolder | 4 | 10uF | Samsung Electro-Mechanics | CL21A106KAYNNNE | Mouser Electronics | 187-CL21A106KAYNNNE | 0.124 | 0,064 | 0,064 | 0,04 | 0,038 | 2-3 DIAS | 2-3 DIAS
 | 2 | C1,C2 | C_0805_2012Metric_Pad1.18x1.45mm_HandSolder | 2 | 20pF | Samsung Electro-Mechanics | CL31A226KAHNNNE | Mouser Electronics | 187-CL31A226KAHNNNE | 0.2 | 0,2 | 0,2 | 0,2 | 0,13 | 2-3 DIAS | 2-3 DIAS
 | 3 | J9,J8,J7 | PinHeader_1x02_P2.54mm_Vertical | 3 | Conn_01x02 | Wurth Elektronik | 61300211121 | Mouser Electronics | 710-61300211121 | 0,124 | 0,107 | 0,075 | 0,062 | 0,062 | 2-3 DIAS | 2-3 DIAS
 | 4 | C4 | C_0805_2012Metric_Pad1.18x1.45mm_HandSolder | 1 | 100uF | Murata Electronics | GRM31CR61A107MEA8L | Mouser Electronics | 81-GRM31CR61A107MA8L | 0,475 | 0,29 | 0,29 | 0,146 | 0,115 | 2-3 DIAS | 2-3 DIAS
 | 5 | R11,R3,R1,R9,R2,R12 | R_0805_2012Metric_Pad1.20x1.40mm_HandSolder | 6 | 10k | Yageo | RC0805FR-0710KL | Mouser Electronics | 603-RC0805FR-0710KL | 0,133 | 0,015 | 0,015 | 0,007 | 0,004 | 2-3 DIAS | 2-3 DIAS
 | 6 | SW1 | SW_PUSH_6mm | 1 | SW_Push | Omron | B3F-1000 | Mouser Electronics | 653-B3F-1000 | 0,238 | 0,178 | 0,178 | 0,162 | 0,134 | 2-3 DIAS | 2-3 DIAS
 | 7 | Y1 | ECS80830JGNTR | 1 | Crystal | ECS | ECS-80-8-30-JGN-TR | Mouser Electronics | 520-ECS-80-8-30JGNTR | 0,532 | 0,423 | 0,423 | 0,343 | 0,28 | 2-3 DIAS | 10 SEMANAS
 | 8 | C20,C19,C17,C18,C13 | C_0603_1608Metric_Pad1.08x0.95mm_HandSolder | 5 | 100nF | Murata Electronics | GCM188R71C104KA37J | Mouser Electronics | 81-GCM188R71C104KA7J | 0,181 | 0,103 | 0,103 | 0,044 | 0,028 | 2-3 DIAS | 2-3 DIAS
 | 9 | D1 | LED_0603_1608Metric | 1 | LED | AMS-Osram | LB Q39G-L2OO-35-1 | Mouser Electronics | 720-LBQ39GL2N2351 | 0,219 | 0,149 | 0,149 | 0,067 | 0,048 | 2-3 DIAS | 2-3 DIAS
 | 10 | H1,H4,H3,H2 | MountingHole_3.2mm_M3 | 4 | MountingHole | x | x | x | x | x | x | x | x | x | x | x
 | 11 | SW4,SW3 | SW_PUSH_6mm | 2 | MPB01-1B33-S-D | Omron | B3F-4050 | Mouser Electronics | 653-B3F-4050 | 0,285 | 0,25 | 0,25 | 0,229 | 0,217 | 2-3 DIAS | 2-3 DIAS
 | 12 | R7 | R_0805_2012Metric_Pad1.20x1.40mm_HandSolder | 1 | 120 | Yageo | RC0805FR-13120RL | Mouser Electronics | 603-RC0805FR-13120RL | 0,095 | 0,013 | 0,013 | 0,01 | 0,004 | 2-3 DIAS | 2-3 DIAS
 | 13 | U4 | REG_LT1117CST-3.3 | 1 | LT1117CST-3.3 | Texas Instruments | LM1117DT-3.3/NOPB | Mouser Electronics | 926-LM1117DT-3.3NOPB | 1,61 | 1,18 | 1,18 | 0,884 | 0,749 | 2-3 DIAS | 18 SEMANAS
 | 14 | J1 | PinHeader_2x04_P2.54mm_Vertical | 1 | Conn_02x04_Odd_Even | Samtec | SSW-104-02-G-S | Mouser Electronics | 200-SSW10402GS | 1,33 | 1,33 | 1,17 | 0,741 | 0,741 | 2-3 DIAS | 1 SEMANA
 | 15 | JP1 | PinHeader_1x03_P2.54mm_Vertical | 1 | Jumper_3_Bridged12 | Samtec | TSW-103-07-G-S | Mouser Electronics | 200-TSW10307GS | 0,257 | 0,257 | 0,257 | 0,204 | 0,096 | 2-3 DIAS | 2-3 DIAS
 | 16 | U2 | SOIC127P1032X265-20N | 1 | L293DD | Texas Instruments | DRV8231ADDAR | Mouser Electronics | 595-DRV8231ADDAR | 1,24 | 0,897 | 0,813 | 0,599 | 0,558 | 2-3 DIAS | 6 SEMANAS
 | 17 | R10 | R_0805_2012Metric_Pad1.20x1.40mm_HandSolder | 1 | 1k | Yageo | RC0805FR-071KL | Mouser Electronics | 603-RC0805FR-071KL | 0,095 | 0,011 | 0,011 | 0,007 | 0,004 | 2-3 DIAS | 2-3 DIAS
 | 18 | U1 | QFN65P600X600X100-29N | 1 | PIC18F2580-I_ML | Microchip | PIC18F2580-I/SO | Mouser Electronics | 579-PIC18F2580-I/SO | 7,72 | 7,72 | 7,72 | 7,72 | 7,72 | 2-3 DIAS | 5 SEMANAS
 | 19 | SW2 | SW_DIP_SPSTx01_Slide_6.7x4.1mm_W7.62mm_P2.54mm_LowProfile | 1 | SW_DIP_x01 | Wurth Elektronik | 418117170906 . | Mouser Electronics | 710-418117170906 | 2,02 | 1,84 | 1,84 | 1,47 | 1,24 | 2-3 DIAS | 6 SEMANAS
 | 20 | J3 | PinSocket_1x06_P2.54mm_Vertical | 1 | Conn_PIC_ICSP_ICD | Wurth Elektronik | 61300611121 | Mouser Electronics | 710-61300611121 | 0,333 | 0,283 | 0,197 | 0,162 | 0,162 | 2-3 DIAS | 2 SEMANAS
 | 21 | J2 | DB9 | 1 | DE9_Pins | Moler | 172704-0077 | Mouser Electronics | 152-172704-0077 | 4,67 | 3,27 | 3,05 | 2,76 | 2,76 | 2-3 DIAS | 15 SEMANAS
 | 22 | U3 | SOIC-8_3.9x4.9mm_P1.27mm | 1 | TCAN332D | Texas Instruments | TCAN332D | DigiKey | 296-49938-ND | 2,51 | 1,87 | 1,56627 | 1,398 | 1,28938 | 2-3 DIAS | 6 SEMANAS
 |  |  |  |  |  |  |  | Coste unitario PCBs | : | 26,885 | 21,793 | 20,843 | 18,140 | 17,097 | : euros
 |  |  |  |  |  |  |  | Coste total PCBs | : | 26,885 | 217,93 | 1042,164 | 18139,00 | 341927,6 | : euros
 |  |  |  |  |  |  |  | Coste Fabricación PCBs (Stencil): |  | 4,56 | 10,57 | 21,58 | 162,93 | 2606,34 | : euros
 |  |  |  |  |  |  |  | Coste Fabricación PCBs (Turnkey): |  | 3,91 | 7,46 | 15,79 | 84,20 | 1346,53 | : euros

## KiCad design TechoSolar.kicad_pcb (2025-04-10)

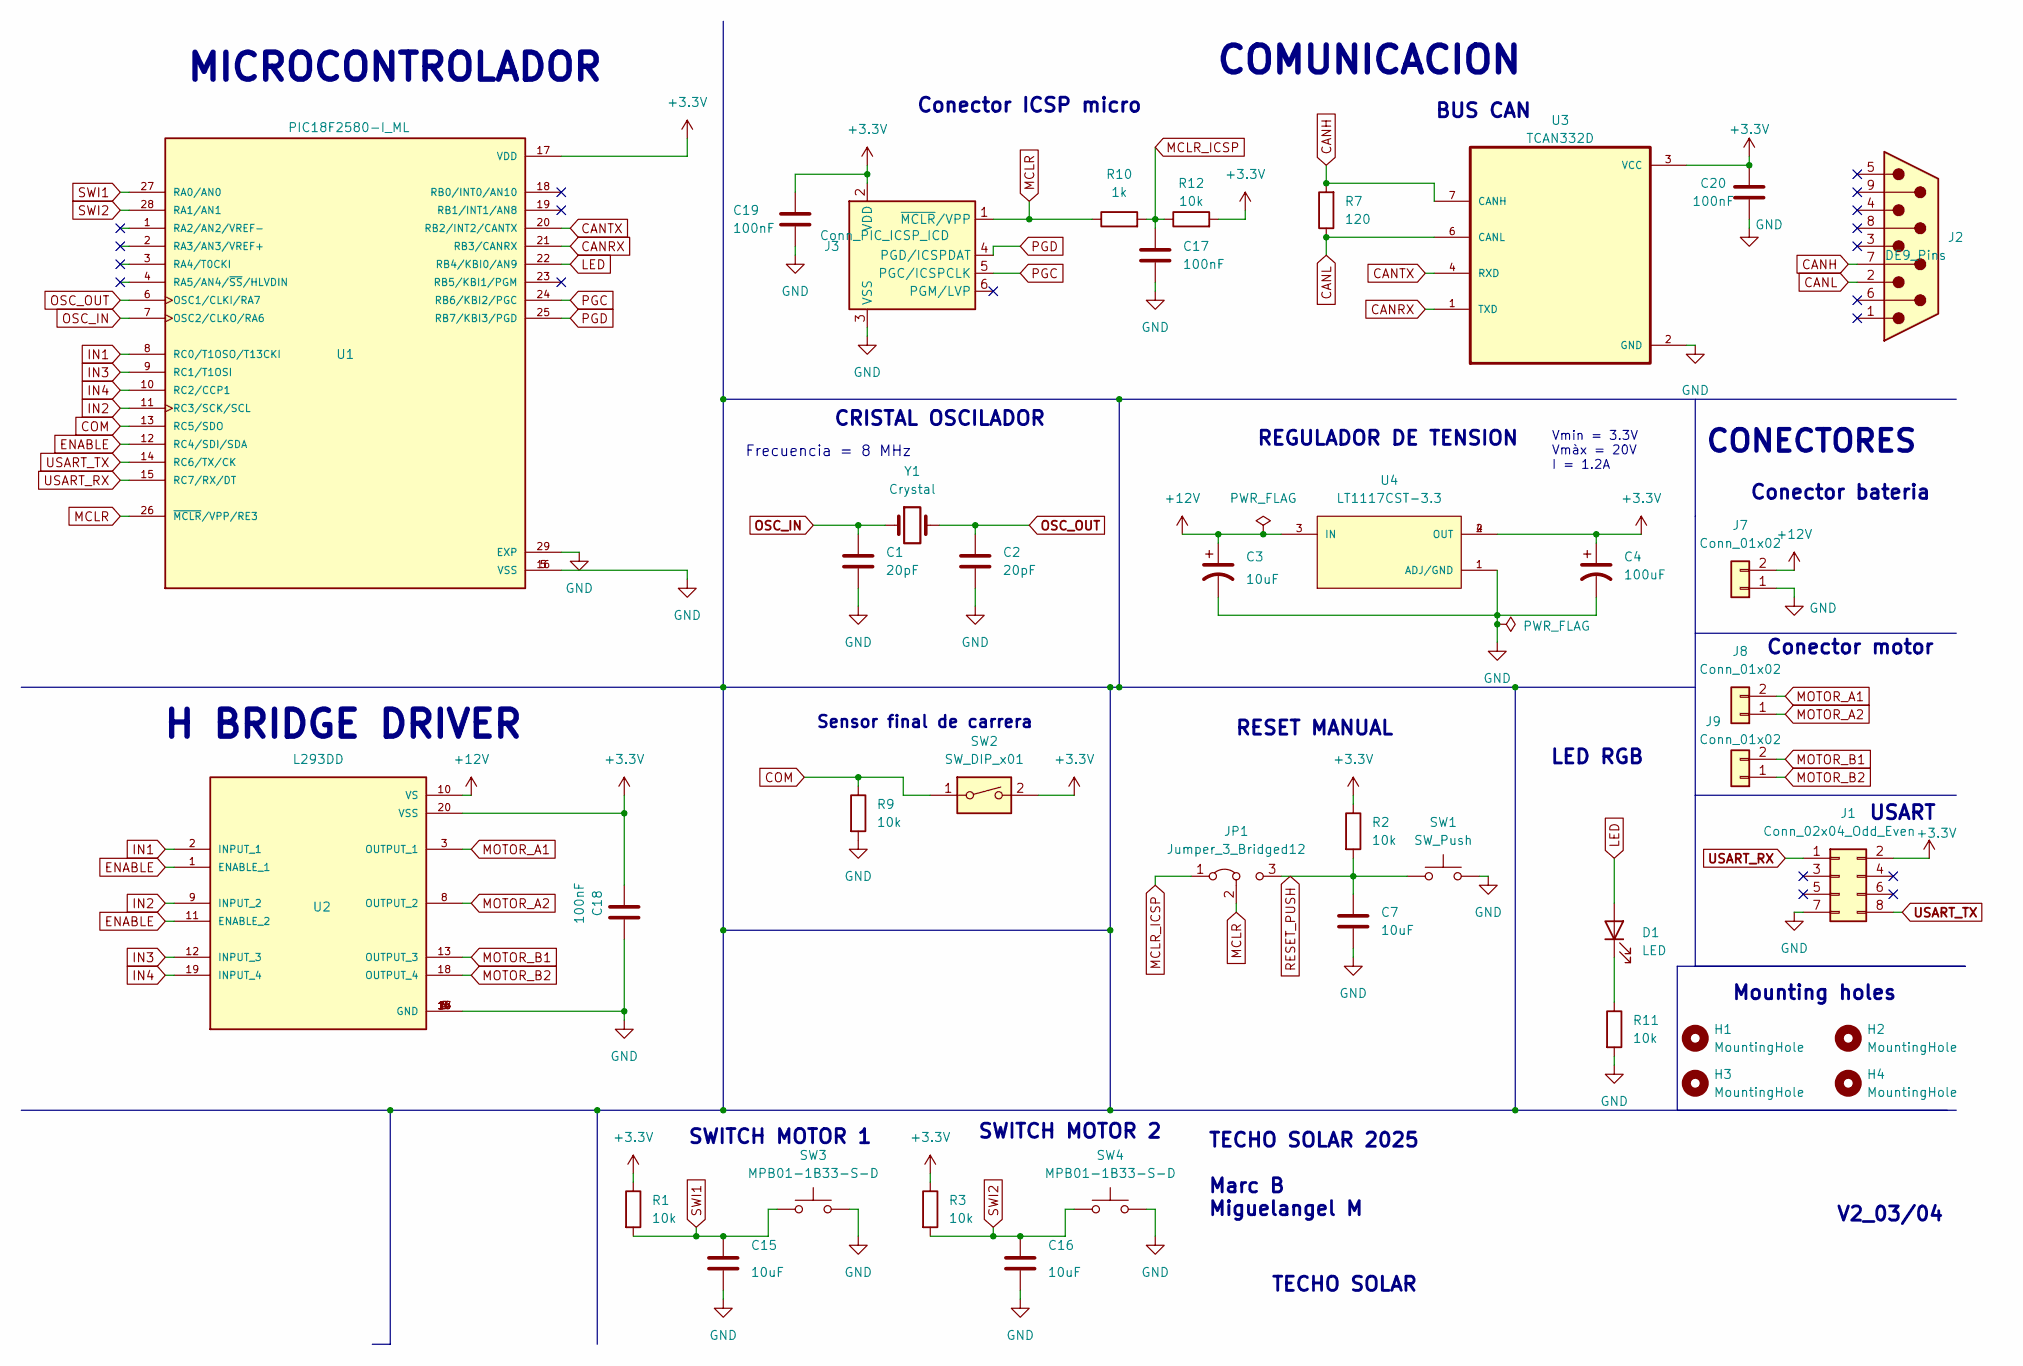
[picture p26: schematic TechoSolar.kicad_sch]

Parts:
C1, C2: 20pF; C_0805_2012Metric_Pad1.18x1.45mm_HandSolder
C3, C7, C15, C16: 10uF; C_0805_2012Metric_Pad1.18x1.45mm_HandSolder
C4: 100uF; C_0805_2012Metric_Pad1.18x1.45mm_HandSolder
C17, C18, C19, C20: 100nF; C_0603_1608Metric_Pad1.08x0.95mm_HandSolder
D1: LED; LED_0603_1608Metric
H1, H2, H3, H4: MountingHole; MountingHole_3.2mm_M3
J1: Conn_02x04_Odd_Even; PinHeader_2x04_P2.54mm_Vertical
J2: DE9_Pins; DB9
J3: Conn_PIC_ICSP_ICD; PinSocket_1x06_P2.54mm_Vertical
J7, J8, J9: Conn_01x02; PinHeader_1x02_P2.54mm_Vertical
JP1: Jumper_3_Bridged12; PinHeader_1x03_P2.54mm_Vertical
R1, R2, R3, R9, R11, R12: 10k; R_0805_2012Metric_Pad1.20x1.40mm_HandSolder
R7: 120; R_0805_2012Metric_Pad1.20x1.40mm_HandSolder
R10: 1k; R_0805_2012Metric_Pad1.20x1.40mm_HandSolder
SW1: SW_Push; SW_PUSH_6mm
SW2: SW_DIP_x01; SW_DIP_SPSTx01_Slide_6.7x4.1mm_W7.62mm_P2.54mm_LowProfile
SW3, SW4: MPB01-1B33-S-D; SW_PUSH_6mm
U1: PIC18F2580-I_ML; QFN65P600X600X100-29N; PARTREV D
U2: L293DD; SOIC127P1032X265-20N; PARTREV N/A
U3: TCAN332D; SOIC127P599X175-8N
U4: LT1117CST-3.3; REG_LT1117CST-3.3
Y1: Crystal; ECS80830JGNTR

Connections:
+3.3V: C4.1, C18.2, C19.1, C20.2, J1.2, J3.2 (VDD), R1.1, R2.1, R3.1, R12.2, SW2.2, U1.17 (VDD), U2.20 (VSS), U3.3 (VCC), U4.2 (OUT), U4.4 (OUT); also elsewhere on the board
+12V: C3.1, J7.2, U2.10 (VS), U4.3 (IN)
CANH: J2.7, R7.2, U3.7 (CANH)
CANL: J2.2, R7.1, U3.6 (CANL)
CANRX: U1.21 (RB3/CANRX), U3.1 (TXD)
CANTX: U1.20 (RB2/INT2/CANTX), U3.4 (RXD)
COM: R9.1, SW2.1, U1.13 (RC5/SDO)
ENABLE: U1.12 (RC4/SDI/SDA), U2.1 (ENABLE_1), U2.11 (ENABLE_2)
GND: C1.2, C2.2, C3.2, C4.2, C7.2, C15.2, C16.2, C17.2, C18.1, C19.2, C20.1, J1.7, J3.3 (VSS), J7.1, R9.2, R11.2, SW1.2, SW3.2, SW4.2, U1.5 (VSS), U1.16 (VSS), U1.29 (EXP), U2.4 (GND), U2.5 (GND), U2.6 (GND), U2.7 (GND), U2.14 (GND), U2.15 (GND), U2.16 (GND), U2.17 (GND), U3.2 (GND), U4.1 (ADJ/GND); also elsewhere on the board
IN1: U1.8 (RC0/T1OSO/T13CKI), U2.2 (INPUT_1)
IN2: U1.11 (RC3/SCK/SCL), U2.9 (INPUT_2)
IN3: U1.9 (RC1/T1OSI), U2.12 (INPUT_3)
IN4: U1.10 (RC2/CCP1), U2.19 (INPUT_4)
LED: D1.2 (A), U1.22 (RB4/KBI0/AN9)
MCLR: J3.1 (~MCLR/VPP), JP1.2 (C), R10.1, U1.26 (~MCLR/VPP/RE3)
MCLR_ICSP: C17.1, JP1.1 (A), R10.2, R12.1
MOTOR_A1: J8.2, U2.3 (OUTPUT_1)
MOTOR_A2: J8.1, U2.8 (OUTPUT_2)
MOTOR_B1: J9.2, U2.13 (OUTPUT_3)
MOTOR_B2: J9.1, U2.18 (OUTPUT_4)
unnamed: D1.1 (K), R11.1
OSC_IN: C1.1, U1.7 (OSC2/CLKO/RA6), Y1.1
OSC_OUT: C2.1, U1.6 (OSC1/CLKI/RA7), Y1.2
PGC: J3.5 (PGC/ICSPCLK), U1.24 (RB6/KBI2/PGC)
PGD: J3.4 (PGD/ICSPDAT), U1.25 (RB7/KBI3/PGD)
RESET_PUSH: C7.1, JP1.3 (B), R2.2, SW1.1
SWI1: C15.1, R1.2, SW3.1, U1.27 (RA0/AN0)
SWI2: C16.1, R3.2, SW4.1, U1.28 (RA1/AN1)
USART_RX: J1.1, U1.15 (RC7/RX/DT)
USART_TX: J1.8, U1.14 (RC6/TX/CK)

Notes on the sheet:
V2_03/04
BUS CAN
Vmin = 3.3V Vmàx = 20V I = 1.2A
MICROCONTROLADOR
COMUNICACION
TECHO SOLAR
SWITCH MOTOR 1
LED RGB
CRISTAL OSCILADOR
Frecuencia = 8 MHz
CONECTORES
RESET MANUAL
SWITCH MOTOR 2
TECHO SOLAR 2025 Marc B Miguelangel M
Conector bateria
Conector ICSP micro
Sensor final de carrera
Conector motor
H BRIDGE DRIVER
REGULADOR DE TENSION
USART
Mounting holes

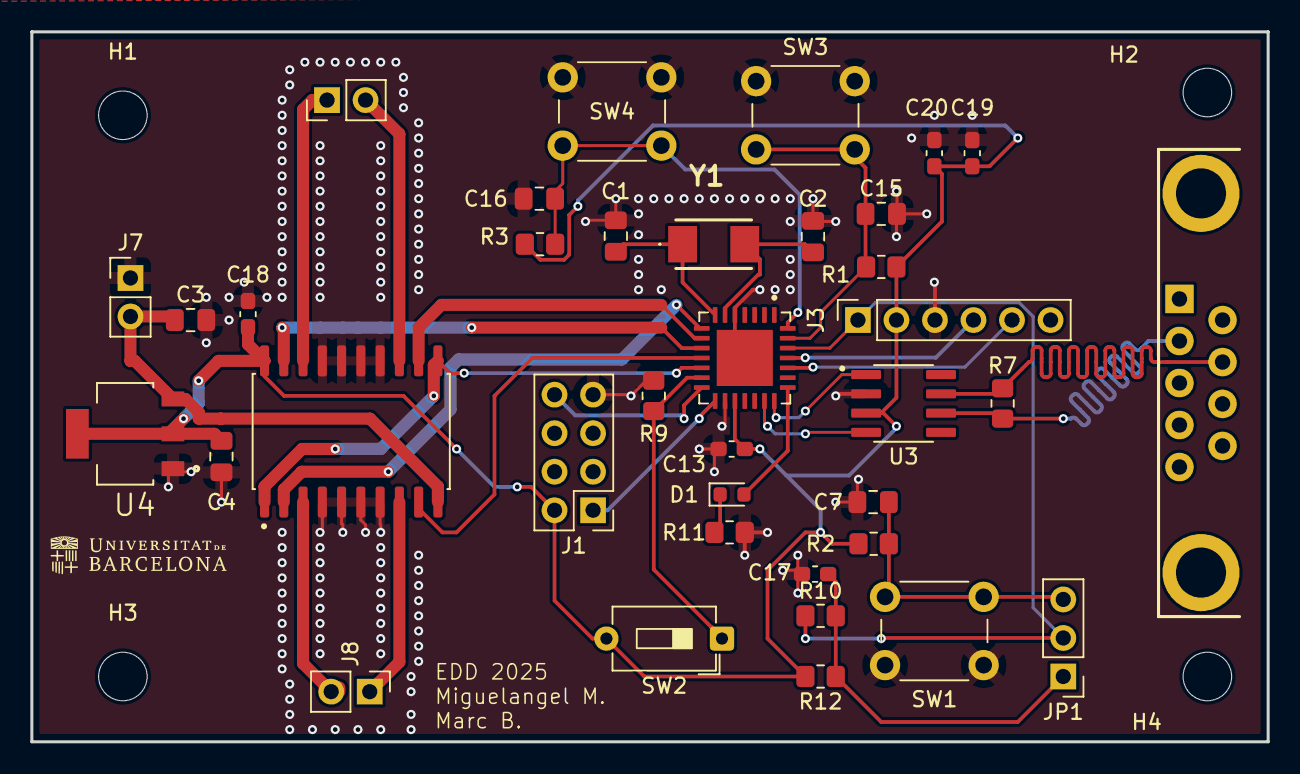
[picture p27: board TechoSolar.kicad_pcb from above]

Board: 2 copper layers, 81.5 x 46.8 mm, 41 parts (0 on the bottom side), 30 nets.

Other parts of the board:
C13: 100nF; C_0603_1608Metric_Pad1.08x0.95mm_HandSolder

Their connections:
+3.3V: C13.2; also elsewhere on the board
GND: C13.1; also elsewhere on the board

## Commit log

2025-03-23 Elimino estos 2 archivos de prubea README
2025-03-27 Upload Esquematico_TechoSolar
    [TechoSolar.kicad_sch]
2025-04-02 Añadiendo Layout circuito
    [TechoSolar.kicad_pcb]
2025-04-03 Simulacion de opamp
2025-04-10 Create Reglas de Diseño
